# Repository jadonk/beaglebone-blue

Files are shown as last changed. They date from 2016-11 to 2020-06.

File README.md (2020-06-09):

# BeagleBoard.org BeagleBone Blue
_BeagleBone optimized for robotics and machine control_

Home on Github: https://github.com/beagleboard/beaglebone-blue



To optimize BeagleBone for education, BeagleBone Blue was created that integrates many components for robotics and machine control, including connectors for off-the-shelf robotic components. For education, this means you can quickly start talking about topics such as programming and control theory, without needing to spend so much time on electronics. The goal is to still be very hackable for learning electronics as well, including being fully open hardware.

BeagleBone Blue's legacy is primarily from contributions to BeagleBone Black robotics by [UCSD Flow Control and Coordinated Robotics Lab](http://robotics.ucsd.edu/), [Strawson Design](http://www.strawsondesign.com/), [Octavo Systems](http://octavosystems.com), [WowWee](http://www.wowwee.com/mip/), [National Instruments LabVIEW](http://www.ni.com/labview/) and of course the [BeagleBoard.org Foundation](https://beagleboard.org/about).

# Terms
These design materials are *NOT SUPPORTED* and *DO NOT* constitute a reference design. Only “community” support is allowed via resources at [BeagleBoard.org/discuss](https://beagleboard.org/discuss).

THERE IS NO WARRANTY FOR THE DESIGN MATERIALS, TO THE EXTENT PERMITTED BY APPLICABLE LAW. EXCEPT WHEN OTHERWISE STATED IN WRITING THE COPYRIGHT HOLDERS AND/OR OTHER PARTIES PROVIDE THE DESIGN MATERIALS “AS IS” WITHOUT WARRANTY OF ANY KIND, EITHER EXPRESSED OR IMPLIED, INCLUDING, BUT NOT LIMITED TO, THE IMPLIED WARRANTIES OF MERCHANTABILITY AND FITNESS FOR A PARTICULAR PURPOSE. THE ENTIRE RISK AS TO THE QUALITY AND PERFORMANCE OF THE DESIGN MATERIALS IS WITH YOU. SHOULD THE DESIGN MATERIALS PROVE DEFECTIVE, YOU ASSUME THE COST OF ALL NECESSARY SERVICING, REPAIR OR CORRECTION.

In other words, you may use the design materials as you choose and there is no license with regards to usage in the manufacturing process. We mean it, these design materials may be totally unsuitable for any purposes. Don't blame us!

As a general rule, we don't encourage use of this or other off-the-shelf single board computers in commercial products without engaging with a manufacturer to create a supplier agreement and make sure that you can get material as your business demands. Further, we do update the design on occasions where we find it necessary and won't guarantee a supply of older revisions, though we do seek periodic manufacturing of all of our boards for a period of roughly 10 years and will make design changes to replace obsolete parts and that may impact your usage. If you do opt to use it in a product, you take full responsibility for that product.

Do not use the BeagleBoard.org logo or trademarks (such as BeagleBoard and BeagleBone) on your products without a [logo license](https://beagleboard.org/logo) from the BeagleBoard.org Foundation, but feel free to reference BeagleBoard.org.

See the [LICENSE](https://github.com/beagleboard/beaglebone-blue/blob/master/LICENSE) file regarding the copyright of these materials.

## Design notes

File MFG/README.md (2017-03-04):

# PCB fabrication information
* 1.6 mm PCB thickness
* 1 oz copper thickness on outer layers
* 0.5 oz copper on internal layers
* Solder mask as blue
* Silk print as white

# Files
* bb_blue_4layer.cam - EAGLE CAM script
* BeagleBone_Blue.dri - drill log
* BeagleBone_Blue.gpi - outline log
* BeagleBone_Blue.toplayer.ger - top layer copper
* BeagleBone_Blue.internalplane1.ger - inner layer copper
* BeagleBone_Blue.ingernalplane2.ger - inner layer copper
* BeagleBone_Blue.bottomlayer.ger - bottom layer copper
* BeagleBone_Blue.topsilkscreen.ger - top layer silkscren
* BeagleBone_Blue.bottomsilkscreen.ger - bottom layer silkscren
* BeagleBone_Blue.boardoutline.ger - board outline or mill layer
* BeagleBone_Blue.tcream.ger - top layer solder paste
* BeagleBone_Blue.bcream.ger - bottom layer solder paste
* BeagleBone_Blue.topsoldermask.ger - top layer soldermask
* BeagleBone_Blue.bottomsoldermask.ger - bottom layer soldermask
* BeagleBone_Blue.drills.xln - drill file

# Conformal coating application areas

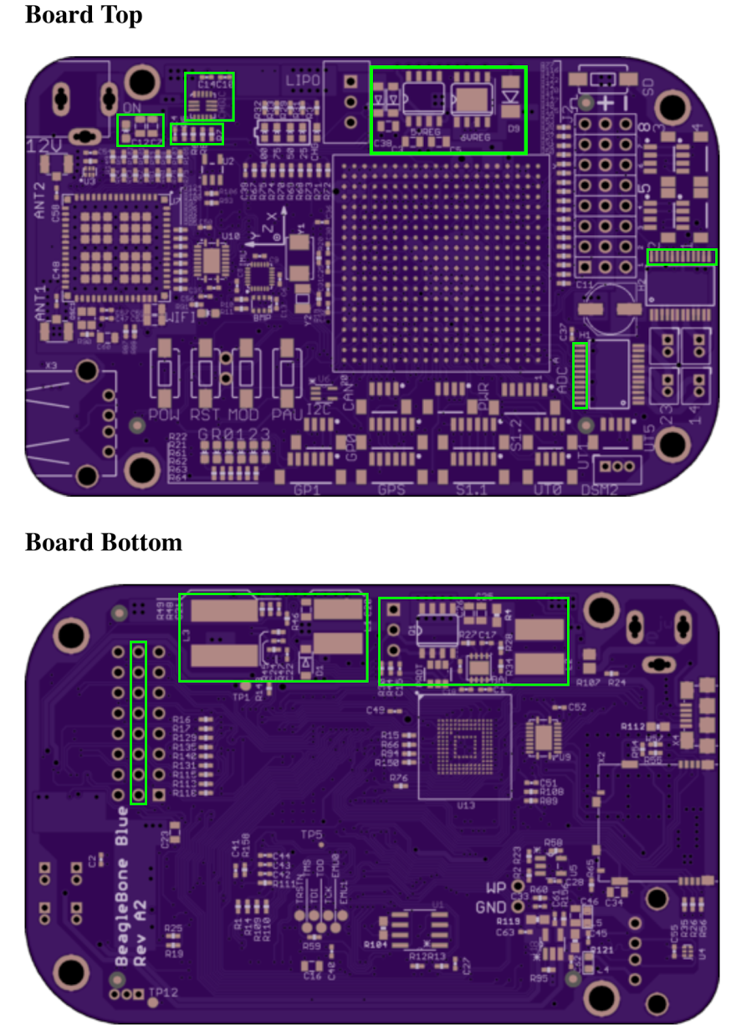
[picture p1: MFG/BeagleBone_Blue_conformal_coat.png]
Image showing conformal coated areas


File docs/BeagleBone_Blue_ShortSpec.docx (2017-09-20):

BeagleBone™ Blue is based on the extremely successful open-source hardware design of BeagleBone™ Black, a high-expansion, maker-focused, community-supported open hardware computer, created by the BeagleBoard.Org Foundation. BeagleBone™ Blue combines the high-performance flexible WiFi/Bluetooth WiLink™ interface of the BeagleBone™ Black Wireless and the robotics capabilities of the Robotics Cape from Strawson Design. BeagleBone™ Blue has onboard 2 cell (2S) LiPo battery management with charger and battery level LEDs, 8 servo motor outputs, 4 DC motor drivers, 4 quadrature encoder inputs, a wide array of GPIO and serial protocol connectors including CAN, a 9 axis IMU and barometer, 4 ADC inputs, a PC USB interface, an USB 2.0 host port, a reset button, a power button, two user configurable buttons and six indicating LEDs. Built on Octavo Systems’ System-In-Package that integrates a high-performance TI ARM processor and 512MB of DDR3, BeagleBone™ Blue boots Linux in around 10 seconds and gets you started developing through your web browser in less than 5 minutes with just a single USB cable.

Specifications:

  a. Processor (Integrated in the OSD3358):
    i. AM335x 1GHz ARM® Cortex-A8
    ii. SGX530 graphics accelerator
    iii. NEON floating-point accelerator
    iv. 2x PRU 32-bit 200MHz microcontrollers
  b. Memory:
    i. 512MB DDR3 800MHZ RAM (Integrated in the OSD3358)
    ii. 4GB 8-bit eMMC on-board flash storage
    iii. SD/MMC Connector for microSD
  c. Software Compatibility
    i. Debian
    ii. Android
    iii. Ubuntu
    iv. Cloud9 IDE on Node.js w/ BoneScript library
  d. Connectivity
    i. High speed USB 2.0 Client port: Access to USB0, Client mode via microUSB
    ii. High speed USB 2.0 Host port: Access to USB1, Type A Socket, 500mA LS/FS/HS
    iii. WiLink 1835 WiFi 802.11 b/g/n 2.4GHz. Supports the following modes
      1. 2x2 MIMO
      2. AP
      3. SmartConfig
      4. STA
      5. Wi-Fi Direct
      6. Mesh over Wi-Fi based on 802.11s
    iv. WiLink 1835 Bluetooth 4.1 with BLE
    v. Serial port:
      1. UART0, UART1, UART5 available via 4 pin JST connectors
      2. UART2 available via 6 pin JST connector (EM-506 GPS style connector)
      3. UART4 RX available via 3 pin DSM2 connector
    vi. I2C1 available via 4 pin JST connector
    vii. SPI1 CS0 (S1.1) and SPI1 CS1 (S1.2) available via 6 pin JST connectors
    viii. CAN available via 4 pin JST connector (includes TCAN1051 CAN transceiver)
    ix. 8 GPIOs (GP0 and GPI1) available via 6 pin JST connectors
    x. ADC inputs 0 to 3 available via 6 pin JST connector
    xi. 3.3VDC and 5VDC power output via 4 pin JST connector
  e. Power management:
    i. TPS65217C PMIC is used along with a separate LDO to provide power to the system (Integrated in the OSD3358)
    ii. 2 cell (2S) LiPo battery charger (powered by 9 – 18VDC DC Jack)
      1. 4 battery level LEDs
      2. 1 charger LED
    iii. 6VDC 4A regulator to drive servo motor outputs
  f. Debug Support: JTAG test points
  g. Power Source
    i. microUSB USB
    ii. 2 cell (2S) LiPo battery connector
    iii. 9 - 18VDC DC Jack
  h. User Input / Output
    i. Power Button
    ii. Reset Button
    iii. Boot Button
    iv. 2 user configurable buttons
    v. 6 user configurable LEDs; Power LED
  i. Motor Control (requires power from either DC Jack or 2S battery):
    i. 4 DC motor drivers
    ii. 4 Quadrature encoder inputs
    iii. 8 Servo motor outputs
  j. Sensors
    i. 9 axis IMU
    ii. Barometer

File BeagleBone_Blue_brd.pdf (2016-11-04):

# BeagleBone Blue

# BeagleBone optimized for educational robotics

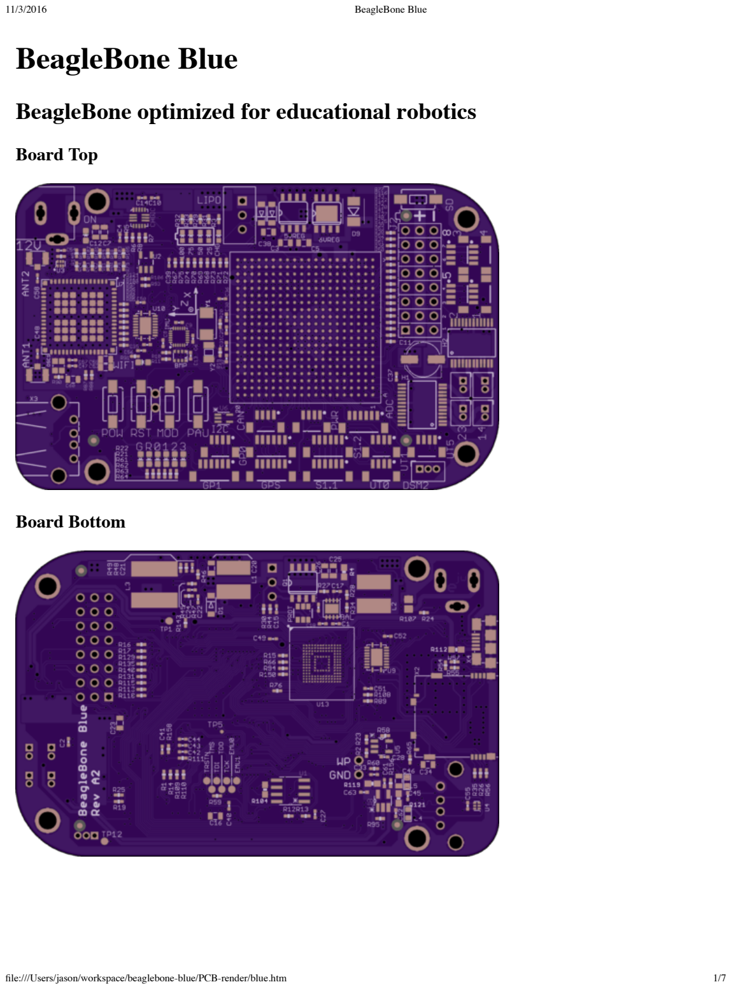
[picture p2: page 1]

11/3/2016 | BeagleBone Blue
file:///Users/jason/workspace/beaglebone-blue/PCB-render/blue.htm | 1/7

# Board Top

# Board Bottom

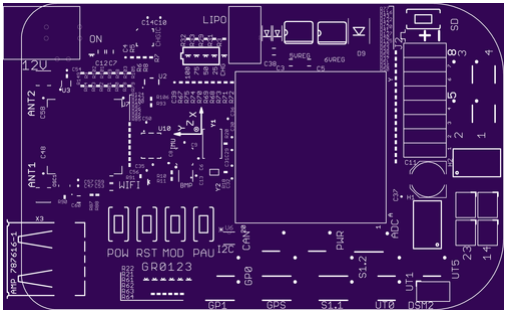
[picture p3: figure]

file:///Users/jason/workspace/beaglebone-blue/PCB-render/blue.htm | 2/7

# Drills

## Rendered from "BeagleBone_Blue.XLN"

# Top Silk Screen

## Rendered from "BeagleBone_Blue.GTO"

file:///Users/jason/workspace/beaglebone-blue/PCB-render/blue.htm | 3/7

# Board Outline

## Rendered from "BeagleBone_Blue.GKO"

file:///Users/jason/workspace/beaglebone-blue/PCB-render/blue.htm | 4/7

# Internal Plane 2

## Rendered from "BeagleBone_Blue.G3L"

# Bottom Silk Screen

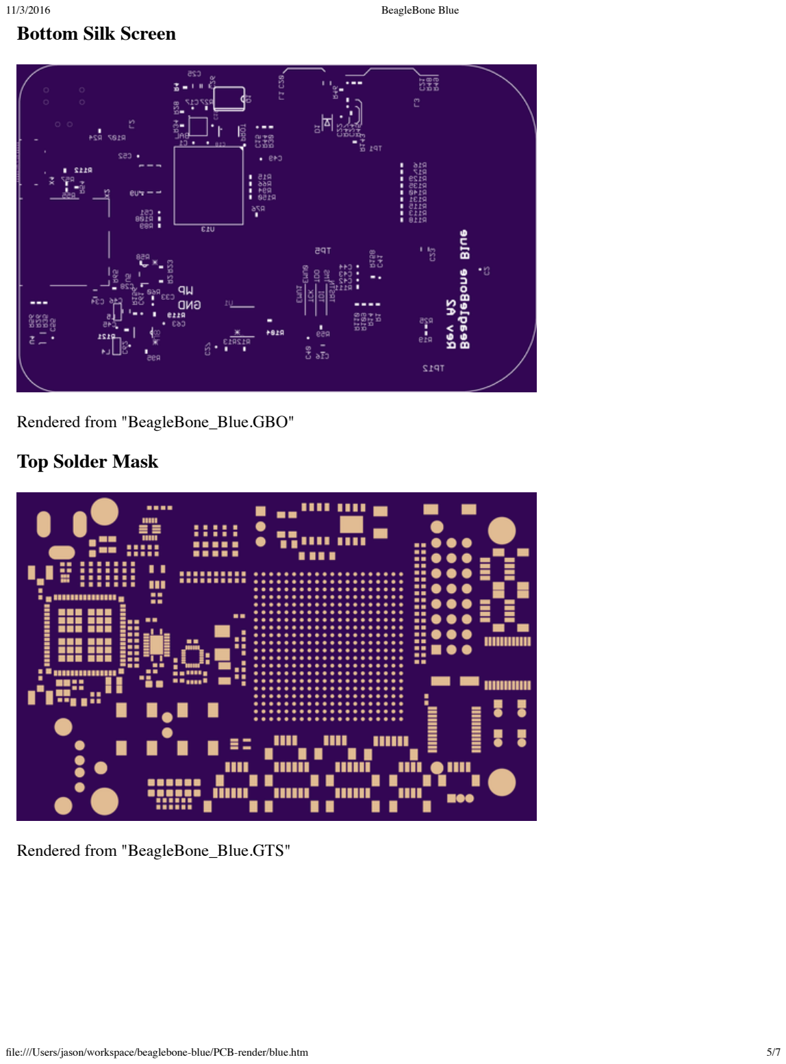
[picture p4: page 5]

file:///Users/jason/workspace/beaglebone-blue/PCB-render/blue.htm | 5/7

## Rendered from "BeagleBone_Blue.GBO"

# Top Solder Mask

## Rendered from "BeagleBone_Blue.GTS"

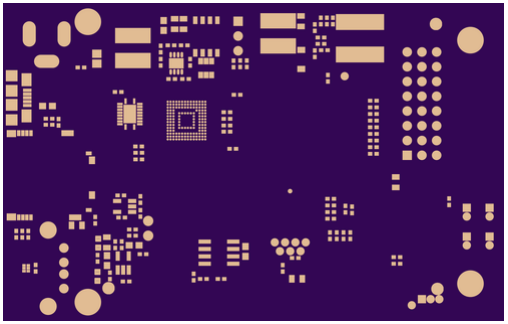
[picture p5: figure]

file:///Users/jason/workspace/beaglebone-blue/PCB-render/blue.htm | 6/7

# Top Layer

## Rendered from "BeagleBone_Blue.GTL"

# Bottom Solder Mask

## Rendered from "BeagleBone_Blue.GBS"

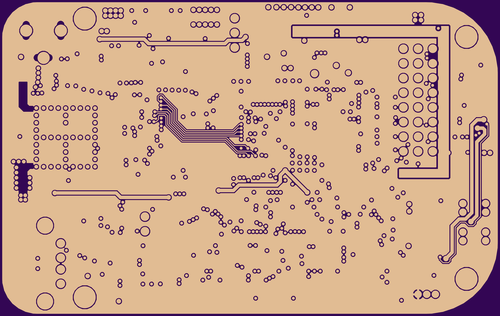
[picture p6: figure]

file:///Users/jason/workspace/beaglebone-blue/PCB-render/blue.htm | 7/7

# Bottom Layer

## Rendered from "BeagleBone_Blue.GBL"

# Internal Plane 1

## Rendered from "BeagleBone_Blue.G2L"

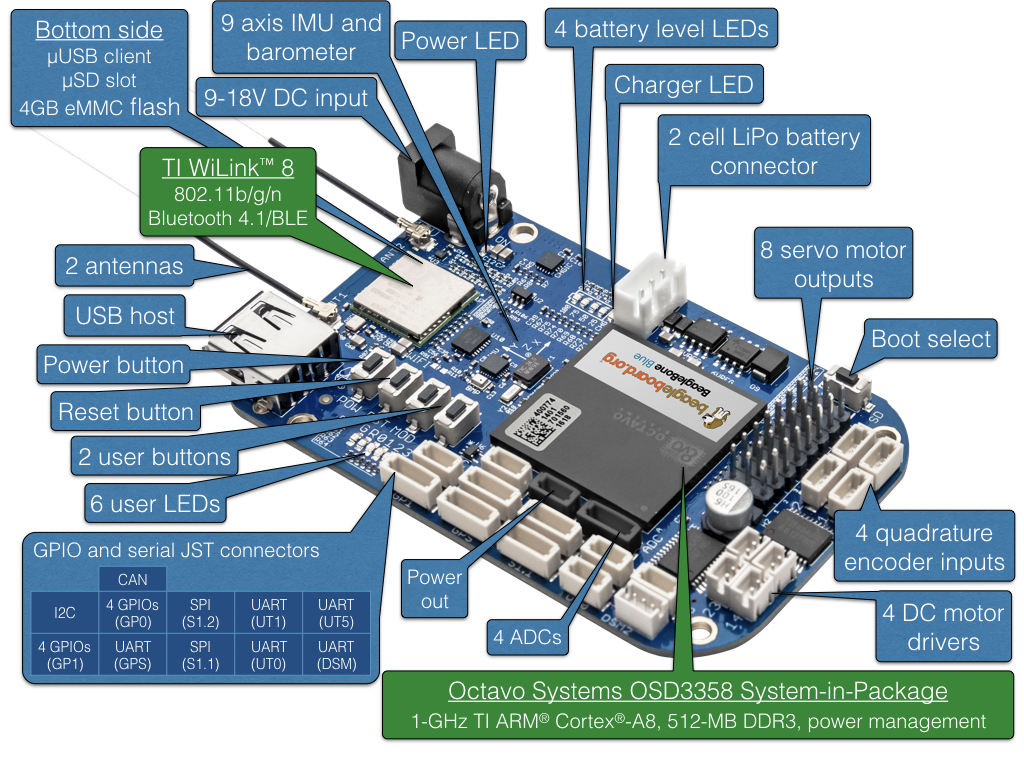
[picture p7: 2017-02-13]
docs/BeagleBone_Blue_balloons.png

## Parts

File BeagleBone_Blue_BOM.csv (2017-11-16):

Qty | Value | Parts | Device | Package | Description | MANUFACTURER AND PART NUMBER | Temperature range / Celsius
5 | BLUE | 0, 1, 2, 3, ON | LED0603 | LED-0603 | LEDs | Lite-On LTST-C191TBKT | -20..80
1 | PJ-102B_POWER_CON | 12V | PJ-102B_POWER_CON | PJ-102B_POWER_CON |  | CUI PJ-102B, MT CONN DC630-20D
1 | AP1509SOIC-8-TIGHT | 5VREG | AP1509SOIC-8-TIGHT | SO08-TIGHT | 150KHz, 2A PWM BUCK DC/DC CONVERTER | Diodes Inc. AP1509-50SG-13 | -20..85
1 | AOZ1284 | 6VREG | AOZ1284 | SO08-EXPOSED |  | Alpha & Omega Semiconductor AOZ1284PI | -40..85
6 | JST_SH_6 | ADC, GP0, GP1, GPS, S1.1, S1.2 | JST_SH_6 | JST_SH_6 |  | JST BM06B-SRSS-TB(LF)(SN), MT CONN WTB10-06-02-2
2 | U.FL-R-SMT-1(10) | ANT1, ANT2 | U.FL-R-SMT-1 | U.FL-R-SMT-1 |  | Hirose U.FL-R-SMT-1(10), MT CONN JTIX-20279
2 | RED | B0, R | LED0603 | LED-0603 | LEDs | Everlight 19-21SURC/S530-A3/TR8, Everlight 19-217/R6C-AL1M2VY/3T
6 | GREEN | B1, B2, B3, CHG, G, WIFI | LED0603 | LED-0603 | LEDs | Everlight 19-21SYGC/S530-E2/TR8, Everlight 19-217/GHC-YR1S2/3T
1 | BQ29209 | BAL | BQ29209 | 8-SON_3X3MM | BQ29209 2-CELL Balance and Overvoltage Protection | Texas Instruments BQ29209DRBR | -40..110
1 | BMP280 | BMP | BMP280 | BMP280 | BOSCH BMP280 Digital Pressure Sensor | Bosch BMP280 | -40..85
32 | 0.1uF | C1, C2, C6, C8, C9, C13, C14, C15, C17, C18, C19, C21, C22, C24, C27, C28, C35, C37, C39, C40, C41, C43, C44, C45, C47, C49, C50, C51, C52, C54, C55, C56 | CAP0402-CAP | 0402-CAP | Capacitor | Samsung CL05A104MP5NNNC, Kemet C0402C104K9PACTU, Murata GRM155R71C104KA88D | -55..85
1 | 100uF 16V | C11 | CPOL-USD | PANASONIC_D | POLARIZED CAPACITOR, American symbol | LELON VES101M1CTR-0605, United Chemi-Con EMVA160ADA101MF55G | -40..85
6 | 10pF | C29, C30, C31, C32, C48, C58 | CAP0402-CAP | 0402-CAP | Capacitor | Yaego CC0402JRNPO9BN100 | -55..125
15 | 10uF | C3, C5, C7, C12, C16, C20, C23, C25, C26, C34, C38, C46, C53, C59, C60 | CAP0805 | 805 | Capacitor | Murata GRM219R61E106KA12D | -55..85
2 | 2.2uF | C33, C36 | CAP0402-CAP | 0402-CAP | Capacitor | TDK C1005X5R0J225K050BC, Murata GRM155R60J225ME15D | -55..85
4 | 1uF | C4, C10, C57, C61 | CAP0402-CAP | 0402-CAP | Capacitor | Samsung CL05A105KO5NNNC, Taiyo Yuden JMK105BJ105KV-F, Murata GRM155R60J105KE19D | -55..85
1 | 1nF | C42 | CAP0402-CAP | 0402-CAP | Capacitor | Murata GRM155R71H102KA01D | -55..85
2 | 0.22uF | C62, C63 | CAP0402-CAP | 0402-CAP | Capacitor | ???
10 | JST_SH_4 | CAN, E1, E2, E3, E4, I2C, PWR, UT0, UT1, UT5 | JST_SH_4 | JST_SH_4_SMD |  | JST BM04B-SRSS-TB(LF)(SN), MT CONN WTB10-04-02-2 | -25..85
1 | MP2615 | CHGIC | MP2615 | MP2615 |  | Monolithic Power Systems MP2615GQ-Z | -40..85
3 |  | D1, D2, D3 | DIODESOD-123 | SOD-123 | Diode | ON Semiconductor MBR230LSFT1G | -55..125
1 |  | D9 | DIODEDO214AA | DO-214AA | Diode | Vishay SSB44-E3/52T | -65..150
1 | JST_ZH_3 | DSM2 | JST_ZH_3 | JST_ZH_3 |  | JST B3B-ZR(LF)(SN), MT CONN WB150SL-03SR03
2 | TB6612FNG | H1, H2 | TB6612FNG | SSOP24 | Toshiba 1A motor driver | Toshiba TB6612FNG(O,C8,EL) | -20..85
1 | MPU-9250 | IMU | MPU-9250 | QFN24G-0.4-3X3MM | 314990005 | Invensense MPU-9250 | -40..105
1 | SERVO_HEADERS_8X | J2 | SERVO_HEADERS_8X | 3X8_0.1_HEADER |  | Preci-Dip 894-80-024-10-001101, Samtec THTSW-108-08-F-T, ??? JTP254-D180-308-001-T | -55..105
2 | 6.8uH | L1, L2 | INDUCTORBOURNS_SRN6045 | SRN6045 | Inductors | Taiyo Yuden NRS6045T6R3MMG | -40..125
1 | 3.6 uH | L3 | INDUCTOR | 8X8MM_INDUCTOR | Inductors | Taiyo Yuden NRS8040T3R6NJGJ | -25..120
2 | 120 | L4, L5 | INDUCTOR/FERRITE-BEAD'0603' | L0603 |  | Laird LI0603G121R-10, Murata BLM18AG121SN1D | -55..125
1 | BATTERY | LIPO | JST_XH_3-PIN | JST_XH_3-PIN |  | MT CONN WB250SV-03SBD03, JST B3B-XH-A(LF)(SN) | -25..85
4 | JST_ZH_2 | M1, M2, M3, M4 | JST_ZH_2 | JST_ZH_2 |  | MT CONN WB150SV-02SBD03, JST B2B-ZR(LF)(SN) | -25..85
5 | SWITCH-MOMENTARY-2SMD-1101NE | MOD, PAU, POW, RST, SD | SWITCH-MOMENTARY-2SMD-1101NE | TACTILE-SWITCH-1101NE | Various NO switches- pushbuttons, reed, etc | C&K Components RS-032G05A3-SM RT | -20..70
1 | NZ2520SB-32.768KHZ-NSA3534C | OSC1 | OSCILLATOR | NZ2520S |  | NDK NZ2520SB-32.768KHZ-NSA3534C, Interquip 1651-L3273-BTKQYA | -40..85
1 | S-8261 | PROT | S-8261 | SOT-236 |  | Seiko S-8261AAJMD-G2JT2G | -40..85
1 | MOSFET-N | Q1 | MOSFET-NCHANNEL | SO08-TIGHT | Common NMOSFET Parts | Vishay Siliconix SI4778DY-T1-GE3 | -55..150
1 | 47k | R45 | RESISTOR0402-RES | 0402-RES | Resistor | Yaego RC0402JR-0747KL | -55..155
2 | 47k 1% | R1, R19 | RESISTOR0402-RES | 0402-RES | Resistor | Yaego RC0402FR-0747KL | -55..155
1 | 120, DNP | R104 | RESISTOR0603 | 0603-RES | Resistor | N/A
1 | .1, 0805 | R107 | R-US_R0805 | R0805 | RESISTOR, American symbol | Yaego RL0805JR-070R1L | -55..125
3 | 0 | R111, R149, R150 | RESISTOR0402-RES | 0402-RES | Resistor | Yaego RC0402JR-070RL | -55..155
1 | 0 | R112 | RESISTOR0603 | 0603-RES | Resistor | Yaego RC0603JR-070RL | -55..155
2 | 0, DNP | R119, R121 | RESISTOR0603 | 0603-RES | Resistor
20 | 33 | R15, R76, R77, R78, R79, R80, R81, R82, R83, R84, R85, R86, R92, R93, R96, R97, R100, R123, R124, R156 | RESISTOR0402-RES | 0402-RES | Resistor | Yaego RC0402JR-0733RL | -55..155
18 | 100k | R16, R17, R47, R87, R88, R113, R115, R116, R118, R120, R122, R125, R127, R129, R131, R135, R140, R143 | RESISTOR0402-RES | 0402-RES | Resistor | Samsung RC1005J104CS, Yaego RC0402JR-07100KL | -55..155
2 | 1M | R18, R20 | RESISTOR0402-RES | 0402-RES | Resistor | Yaego RC0402JR-071ML | -55..155
4 | 1.5K | R2, R23, R58, R106 | RESISTOR0402-RES | 0402-RES | Resistor | Yaego RC0402JR-071K5L | -55..155
8 | 240 | R21, R22, R29, R30, R31, R32, R33, R91 | RESISTOR0402-RES | 0402-RES | Resistor | Yaego RC0603JR-07240RL | -55..155
26 | 10K | R26, R35, R54, R55, R56, R57, R60, R65, R66, R67, R68, R69, R70, R71, R72, R73, R74, R75, R94, R98, R99, R101, R102, R103, R105, R158 | RESISTOR0402-RES | 0402-RES | Resistor | Samsung RC1005J103CS, Yaego RC0402JR-0710KL | -55..155
3 | 150 | R27, R28, R34 | RESISTOR0402-RES | 0402-RES | Resistor | Yaego RC0402JR-07150RL | -55..155
8 | 1k | R3, R44, R46, R61, R62, R63, R64, R90 | RESISTOR0402-RES | 0402-RES | Resistor | Samsung RC1005J102CS, Yaego RC0402JR-071KL | -55..155
1 | 0.1 | R4 | RESISTOR0603 | 0603-RES | Resistor | Samsung RU1608FR100CS, Yaego RL0603FR-070R1L | -55..155
1 | 100k | R47 | RESISTOR0402-RES | 0402-RES | Resistor
1 | 64.9k | R49 | RESISTOR0402-RES | 0402-RES | Resistor | Samsung RC1005F6492CS | -55..155
4 | 10k | R5, R6, R8, R48 | RESISTOR0402-RES | 0402-RES | Resistor
21 | 4.7k | R7, R10, R11, R12, R13, R24, R36, R37, R38, R39, R40, R41, R42, R43, R50, R51, R52, R53, R59, R109, R110 | RESISTOR0402-RES | 0402-RES | Resistor | Samsung RC1005F2610CS, Yaego RC0402JR-074K7L | -55..155
2 | 4.7k 1% | R14, R25 | RESISTOR0402-RES | 0402-RES | Resistor | Samsung RC1005F2610CS, Yaego RC0402FR-074K7L | -55..155
2 | 1K, DNP | R89, R108 | RESISTOR0402-RES | 0402-RES | Resistor | N/A
1 | 10K, DNP | R9 | RESISTOR0402-RES | 0402-RES | Resistor | N/A
1 | OSD3358 | SIP | OSD3358 | OSD3358 | Octavo Systems LLC - OSD3358 Rev A | Octavo Systems OSD3358-512M-BAS | 0..85
1 | TCAN1051HV | U1 | TCAN1051HV | D8 | CAN Transceiver | Texas Instruments TCAN1051HVD | -40..125
1 | EMMC | U13 | EMMC04G-S100-B08U | MICRON_EMMC_153 |  | Micron MTFC4GACAJCN-1M WT, Kingston EMMC04G-S100-B08U | -40..85
1 | SN74LV1T126DBVR | U2 | SN74LV1T126DBVR | SOT23-5 |  | Texas Instruments SN74LV1T126DBVR | -40..125
2 | TPD4S012DRY | U3, U4 | TPD4S012DRYR | SON-6(TI)-DRY |  | Texas Instruments tpd4s012dryr | -40..85
1 | 24LC_32AT-I/OT | U5 | 24LC_32AT-I/OT | SOT95P290X145-5N | IC, I2C Serial EEPROM,SOT-23-5 | Microchip 24LC32AT-I/OT | -40..125
1 | SN74LVC1G07_DCK_5 | U6 | SN74LVC1G07_DCK_5 | DCK5 | Single Buffer/Driver With Open-Drain Output | Texas Instruments SN74LVC1G07DCKR | -40..125
1 | WL1835MODGBMOCR | U7 | WL1835MOD | MOC-100(TI) |  | Texas Instruments WL1835MODGBMOCR | -20..70
1 | TPS2105_DBV_5 | U8 | TPS2105_DBV_5 | DBV5 |  | tps2105_dbv_5 | -40..85
2 | TXS0108ERGYR | U9, U10 | TXS0108ERGYR | R-PVQFN-N20(TI) |  | Texas Instruments TXS0108ERGYR | -40..85
1 | SCHA5B0200 | X2 | SCHA5B0200(ALPS_USD) | SCHA5B0200 |  | Alps SCHA5B0200 | -20..70
1 | USB1 | X3 | USB_HOST_W/CHASSIS_GND | USB_HOST_HORIZONTAL_W/CHASSIS_GND |  | TE Connectivity / AMP 787616-1-P, ??? UBAF-1202 | -55..85
1 | 10118192-0001LF | X4 | 10118192-0001LF | 10118192-0001LF(MICRO-USB-B-AMPHENOL-FCI) | Amphenol FCI Micro USB Type B Complete Surface Mount (SMT) no guide holes | FCI 10118192-0001LF, ??? UBAF-0608 | -30..80
1 | 24 MHz | Y1 | CRYSTAL_5X3.2MM | CRYSTAL_5X3.2MM |  | CTS 445A35A24M00000, TXC 7A-24.000MAAJ-T | -40..85
1 | 32.768kHz | Y2 | CRYSTAL_3.2X1.5 | CRYSTAL_3.2X1.5 |  | Fox Electronics FX135A-327 | -20..70
2 | 2.4GHz antenna |  |  |  |  | Anaren 66089-2406, Gptech GPRC01113-CE0030B5

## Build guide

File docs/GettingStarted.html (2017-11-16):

# Getting Started (Some tips)

## flash firmware

You have probably plugged your board in, and gone to the boards webserver but you want to use something more hands on! 1. Update the firmware to the latest and greatest instructions here (http://192.168.1.7/bone101/Support/BoneScript/updates/) One thing the instructions don't mention is that you need to edit a file in the boot directory in order for the sdcard to be flashed onto the firmware.

1. edit /boot/uEnv on the sdcard.
2. Change ##enable Generic eMMC Flasher: ##make sure, these tools are installed: dosfstools rsync #cmdline=init=/opt/scripts/tools/eMMC/init-eMMC-flasher-v3.sh to ##enable Generic eMMC Flasher: ##make sure, these tools are installed: dosfstools rsync cmdline=init=/opt/scripts/tools/eMMC/init-eMMC-flasher-v3.sh
3. Eject the sdcard from you computer and put it in your Beagle Blue Bone
4. Hold the update button (the one by itself) along with the reset, then let go of the reset, and then the upgrade. This tells the board to boot off the sdcard, with your instruction to flash the sdcard onto the boards firmware.

The flashing only takes a couple of minutes.

## terminal on the board

If you don't have ssh installed, install it. (google is your friend) Then ssh debian@192.168.7.2 The board will tell you what the password is, on my it was temppwd To change your password use the command passwd it will ask you what your current password is, and then ask for the replacement. Then it will say it was too simple and you have to do it again. Normal stuff. If you want to use your simple password, try this.

1. sudo -s

(become superuser/root)

2. enter your password
3. passwd debian
4. exit

(exit from superuser/root)

When you are running as root, passwd is more compliant and will accept simple passwords.

## Want wifi?

On my network, I'm set up as ip 192.168.1.*. To turn your wifi on, do the following.

1. sudo -s

(become superuser/root)

2. cd /etc/network/
3. ifconfig

(Note the wifi inet address, if it is already set, you are done!)

4. connmanctl tether wifi off enable wifi scan wifi services (at this point you should see your network appear along with other stuff, in my case it was "AR Crystal wifi_f45eab2f1ee1_6372797774616c_managed_psk")
5. nano interfaces

(or whatever editor you like)

6. remove the comment # from the wifi lines so it now appears like ##connman: WiFi # connmanctl connmanctl> tether wifi off connmanctl> enable wifi connmanctl> scan wifi connmanctl> services connmanctl> agent on connmanctl> connect wifi_f45eab2f1ee1_6372797774616c_managed_psk connmanctl> quit
7. exit
8. note that you will need to fill in your own network data

## static ip address

You will usually want to have a fixed ip if you are doing robotics, so you have a standard ip to connect to. In my case I wanted 192.168.1.7 to do this,

1. sudo -s
2. connmanctl config wifi_f45eab2f1ee1_6372797774616c_managed_psk --ipv4 manual 192.168.1.7 255.255.255.0 192.168.1.1
3. exit

substitute your own wifi connection of course, and use your own ip as desired.

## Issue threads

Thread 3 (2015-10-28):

Add I/O protection

jadonk, 2015-10-28:
* Add series resistor to I/Os
* Add (DNP) zener diods to I/Os

erikwelsh, 2016-09-27:
Not scheduled to be fixed in any revision.

Closed 2016-10-10.

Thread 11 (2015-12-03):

Add header for UART0

jadonk, 2015-12-03:
* Use a 4-pin JST like the other UART ports.
* No hardware handshaking.

erikwelsh, 2016-09-27:
Rev A1 has a 4-pin JST connector for UART0.

Closed 2016-10-10.

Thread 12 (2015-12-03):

Add series resistors for I/O ports

jadonk, 2015-12-03:

erikwelsh, 2016-09-27:
Same a Issue #3 .  Not scheduled to be fixed in any revision.

Closed 2016-10-10.

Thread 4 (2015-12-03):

Swap UART5_RX and MDIR_2B

jadonk, 2015-12-03:
This is to try to match the UART5 mux. The TI Pin Mux Utility reports an error without this change.

Was the existing wiring verified?

jadonk, 2016-09-20:
Still broken in rev A1.

Closed 2016-11-02.

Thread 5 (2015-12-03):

Adjust SPI1 pins

jadonk, 2015-12-03:
- Use UART0_RTSN (E17) for SPI1_CS0, moving from pin C12.
- Use pin A15 for SPI1_CS1, moving from pin C18.

jadonk, 2016-09-20:
What wasn't noted that I/O set had to have been followed. This will be deferred to Rev B.

erikwelsh, 2016-10-13:
To fix the SPI chip select IO set issue, we will change the location of SPI1 CS0 and CS1.  The final pin mapping will be:

spi1_sclk		A13 (mcasp0_aclkx – current pin)
spi1_d0		B13 (mcasp0_fsx – current pin)
spi1_d1		D12 (mcasp0_axr0 – current pin)
spi1_cs0		H18 (rmii1_refclk – currently unused on BB Blue)
spi1_cs1		C18 (eCAP0_in_PWM0_out – currently GPIO_0_3 on BB Blue)
GPIO_0_3		C12 (currently spi1_cs0)
WIFI_LED		A15 (currently spi1_cs1 - See Issue #29 )

jadonk, 2016-10-13:
There must be an error. How do you have 2 pins be GPIO0_3?

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

erikwelsh, 2016-10-13:
Sorry if I was not clear.  The items in quotes was what the function was on Rev A1a.  Basically, we are taking four pads:  H18, C18, C12 and A15 and swapping around the functionality.  The Rev A2 mapping is outside the quotes.  For example, on Rev A1a GPIO_0_3 (ie GPIO connector 0 pin 3, not AM335 GPIO0_3) was C18.  For Rev A2 it will be C12.

jadonk, 2016-10-16:
@erikwelsh @StrawsonDesign Objections to me changing the net names to reflect the processor GPIO number? I like to avoid people needing to refer to additional documentation in order to program the hardware.

Closed 2016-11-02.

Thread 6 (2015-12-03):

Grab McASP0 for Bluetooth A2DP I2S interface

jadonk, 2015-12-03:
* Move MDIR_1A from U18 to P9_12 (C12) to get MCASP0_ACLKR
* Move LED_2 from V12 to P8_32 (T5) to get MCASP0_FSR
* Move USB1_OCn from T16 to GPIO2_21 (M16) to get MCASP0_AXR0
* Remove HDMICLK_DISn from V17 to get MCASP0_AXR1
* Remove HDMI_INT from U16, just in case I need to get MCASP0_FSX

jadonk, 2016-06-07:
I've confirmed that the McASP connection is not required for connecting to Bluetooth speakers.

erikwelsh, 2016-09-27:
In Rev A1, BT audio signals are hooked up to McASP0 with the following pins:
- MCASP0_ACLKR - pin U18
- MCASP0_FSR - pin V12
- MCASP0_AXR0 - pin T16
- MCASP0_AXR1 - pin V17

The WL183x did not need MCASP0_FSX.  Therefore, it was not connected.

jadonk, 2016-10-10:
BeagleBone Green Wireless .dts file has some info on getting this configured. I'm not sure how to get the device in the right mode to verify this functionality.

Closed 2016-10-10.

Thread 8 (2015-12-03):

Address concerns about connector choice

jadonk, 2015-12-03:
* Could we bundle pig-tails?
  * estimate about $0.10 cost each and likely to bundle about 6 of them
  * 6-wire: https://www.sparkfun.com/products/10361
  * 4-wire: https://www.sparkfun.com/products/9916
  * 2-wire: https://www.sparkfun.com/products/9914
* Where is the documentation for where to buy them?

Why we like them:
* small
* easy to plug and remove
* stay connected well
* readily available

jadonk, 2016-10-12:
We'll have a solution for pigtails and are happy with these connectors.

jiffyjeff, 2022-02-17:
> We'll have a solution for pigtails and are happy with these connectors.

With all due respect, I'd appreciate some assistance locating a bundle of these connectors.

Closed 2016-10-12.

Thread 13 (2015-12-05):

Add CAN PHY and connectors

jadonk, 2015-12-05:

erikwelsh, 2016-09-27:
Rev A1 has CAN PHY (TCAN1051HV) and a JST connector for DCAN1.

jadonk, 2016-10-10:
May need to revisit pin connections. Does that need discussion here before closing this item?

StrawsonDesign, 2016-10-11:
I like the JST connector, think this can be closed.

Dept. Mechanical & Aerospace Engineering
University of California, San Diego

On Mon, Oct 10, 2016 at 11:04 AM, Jason Kridner <notifications@github.com>
wrote:

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

Closed 2016-10-12.

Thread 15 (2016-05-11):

Add connector for additional GPIOs

jadonk, 2016-05-11:

erikwelsh, 2016-09-27:
Rev A1 has two GPIO connectors:
- GPIO0:  4 GPIO pins (JST connector)
- GPIO1: 2 GPIO pins (Grove connector)

GPIO0 uses the following pins (may change in Rev A2):
- Bit 0:  Pin U16 - GPIO1_25
- Bit 1:  Pin V14 - GPIO1_17
- Bit 2:  Pin D13 - GPIO3_20
- Bit 3:  Pin C18 - GPIO0_7

GPIO1 uses the following pins (may change in Rev A2):
- Bit 0:  Pin J15 - GPIO3_2
- Bit 1:  Pin H17 - GPIO3_1

Closed 2016-10-10.

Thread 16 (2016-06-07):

Make new connectors as JST instead of Grove

jadonk, 2016-06-07:

jadonk, 2016-07-19:
Done as part of 57fd393b58db450caf035d6a3a34a7a32e0dd2d6

erikwelsh, 2016-09-27:
Rev A1 has Grove connectors for:
- UART5 (broken due to IOSet issue)
- I2C1
- GPIO (2 pins)

jadonk, 2016-10-12:
Move to JST connectors to save board space and collapse component list.

erikwelsh, 2016-11-01:
Changed UART5 and I2C1 to 4 pin JST connectors.
Changed GPIO1 to a 6 pin JST connector (includes 2 GPIO pins as well as the Red and Green LED signals)

Scalpel78, 2017-03-17:
What is the type of JST connector used called?

StrawsonDesign, 2017-03-17:
All the little I2C, UART, GPIO, SPI, Encoder, and CAN connectors are JST SH, 4 or 6 pin.

Closed 2016-11-02.

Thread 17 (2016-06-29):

Convert client port to OTG

jadonk, 2016-06-29:

jadonk, 2016-06-29:
Use 100mA FET based on ID signal to provide power.

erikwelsh, 2016-09-27:
Not done in Rev A1.

jadonk, 2020-06-09:
Issue migrated to beagleboard/beaglebone-blue#47

Closed 2020-06-09.

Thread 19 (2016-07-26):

Place XYZ silkscreen

jadonk, 2016-07-26:

erikwelsh, 2016-09-27:
Currently, on Rev A1.  Can be closed.

jadonk, 2016-10-10:
It is still a bit small, but it is probably the best we can do.

Closed 2016-10-10.

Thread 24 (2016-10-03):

Change barrel jack from 2.5x5.5mm to 2.1x5.5mm

StrawsonDesign, 2016-10-03:
2.5x5.5mm barrel jacks are far less common than the 2.1x5.5mm standard and are incompatible with the DC adapters found on Sparkfun.com, ebay, and amazon.

jadonk, 2016-10-12:
Error was only on the hand-made prototype. E14 prototypes have the right connector.

Closed 2016-10-12.

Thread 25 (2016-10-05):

Change connection and color of WiFi EN LED

jadonk, 2016-10-05:
It would be easier to identify the WiFi EN and BT EN LEDs if the BT LED was blue and the WiFi LED was green/yellow or some other color. Since we already have green LEDs on the board, perhaps that would be best.

Are these LEDs really all that useful if they are always on? They were helpful for initial debug, but it seems adding additional GPIO LEDs that could be bound to actual network state/activity would be more useful if other GPIOs can be found.

jadonk, 2016-10-12:
Duplicate with #29

Closed 2016-10-12.

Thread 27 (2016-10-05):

Grove connector is wrong part number

jadonk, 2016-10-05:
The JST connectors are not compatible with the Grove cables. Seeed Studio has quoted some SMD versions of their connector.

jadonk, 2016-10-12:
We'll move to smaller JST connectors and use an adapter wire harness.

Closed 2016-10-12.

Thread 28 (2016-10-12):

Are alternate colors available for the JST connectors?

jadonk, 2016-10-12:
This would be to assist in new users locating specific connectors.

erikwelsh, 2016-11-01:
Here is the color scheme for the connectors:

2 pin
M1-4: (4x) white

3 pin
DSM2: (1x) white

4 pin
E1-4, I2C: (5x) white
UT0, UT1, UT5: (3x) black
PWR: (1x) new color #1 (red preferred)
CAN: (1x) new color #2 (green preferred)

6 pin
S1.1, S1.2: (2x) white
GP0-1: (2x) black
ADC: (1x) new color #1 (red preferred)
GPS: (1x) new color #2 (green preferred)

Unfortunately, the colored connectors are a 50% premium over the other connectors so one goal of the above scheme was to minimize the number of colored connectors.

jadonk, 2016-11-15:
If the only secondary color we have is black, let's use white on everything except using black on PWR and ADC. Those are the ones most likely to damage something if connected mistakenly.

cstiegman, 2016-11-15:
Got it - thanks!

Regards,
Craig Stiegman
element14
(773) 90<tel:(773)%20907-5941>7-5941<tel:(773)%20907-5941>

On Nov 15, 2016, at 11:35 AM, Jason Kridner <notifications@github.com<mailto:notifications@github.com>> wrote:

If the only secondary color we have is black, let's use white on everything except using black on PWR and ADC. Those are the ones most likely to damage something if connected mistakenly.

—
You are receiving this because you are subscribed to this thread.
Reply to this email directly, view it on GitHub<https://github.com/jadonk/beaglebone-blue/issues/28#issuecomment-260709970>, or mute the thread<https://github.com/notifications/unsubscribe-auth/AHehhCeqBfeAYJ8UB_gX4odB07LfG4oXks5q-e0EgaJpZM4KVMYC>.
********************************Disclaimer***********************************
The preceding e-mail message (including any attachments) contains information
that may be confidential, be protected by the attorney-client
or other applicable privileges, or constitute non-public information. It
is intended to be conveyed only to the designated recipient(s). If you are
not an intended recipient of this message, please notify the sender by
replying to this message and then delete it from your system. Use,
dissemination, distribution, or reproduction of this message by unintended
recipients is not authorized and may be unlawful.
*****************************************************************************

winsurfwon, 2018-03-16:
Is there a list of all male connectors for all the BB Blue, and is there any MFG that actually sell a set of them minus the power connectors and USB.  It is well specified in the glossy print, but not the actual male mfg connector lead part numbers if one exists.  I called a few but they were not ready for it. So good so far.

jadonk, 2020-06-09:
Issue migrated to beagleboard/beaglebone-blue#52

Closed 2020-06-09.

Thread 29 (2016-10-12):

Change WL_EN LED color to green

jadonk, 2016-10-12:

jadonk, 2016-10-12:
Also, move this LED to the last GPIO rather than WL_EN and make it a general "network connection status" LED.

erikwelsh, 2016-11-01:
Moved WIFI LED to pin A15 (GPIO0_19).  Changed color to Green.

Closed 2016-11-02.

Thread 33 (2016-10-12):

Adjust to fit in Altoid's tin

jadonk, 2016-10-12:

erikwelsh, 2016-11-01:
Moved power connector in as much as possible.  I think it should fit but will not know until we get the A2 boards back.

jadonk, 2016-11-02:
Still would like to find a shorter power connector.

jadonk, 2016-11-07:
I've ordered some PCBs from OSH Park to do a mechanical mock-up to verify the fix. I've not identified a source of a shorter power connector.

jonnycowboy, 2016-11-16:
Would implementing issue 39 (new BMS) allow us to use a different power connector? Is the barrel jack currently used to charge the battery or is it used for directly powering the processor?
https://github.com/jadonk/beaglebone-blue/issues/39

StrawsonDesign, 2016-11-17:
The barrel jack is primarily for charging the battery but can provide power to the 5V regulator when no battery is connected. We picked this connector because of how ubiquitous 12v wallwarts are with this 5.5mm barrel jack. I just wish there were half-length jacks available.

jadonk, 2016-12-08:
I've not been able to find a shorter jack, which is very surprising to me.

A2 still does NOT fit in an Altoids tin. :-(

jadonk, 2017-02-09:
@StrawsonDesign For rev B, can we switch the power input to a JST connector?

https://www.sparkfun.com/products/8734

I wonder how much it would cost to include that in the kit. :-/

StrawsonDesign, 2017-02-10:
Hmmmm, sorry but I really really like the universal barrel jack. We would
get so much pushback from people complaining about needing dedicated
adapters just to charge the thing just like Apple gets with their headphone
jack adapters. I do adore the Altoids tin concept, don't get me wrong! But
in practice I don't think anyone is running their board in a conductive
tin, whereas everyone will need to charge it and everyone with a wifi
router has one of these 12v dc wallwarts in their home already.

Charging via a 9v or 12v capable USB-C connector may get initial pushback
too but at least that's looking a bit more towards a future universal
standard.

Respectfully,
James

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

jadonk, 2020-06-09:
Issue migrated to beagleboard/beaglebone-blue#50

Closed 2020-06-09.

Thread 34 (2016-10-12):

USB host won't work when powered over USB client

jadonk, 2016-10-12:

Closed 2016-10-12.

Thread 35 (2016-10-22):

Change 6V_REG soft-start cap to 0.1uf

StrawsonDesign, 2016-10-22:
6V_REG works on cape but only starts when no load is present on Blue. Cause is likely the 1nF capacitor C21 on Blue. Should change to 0.1uF to match cape.

erikwelsh, 2016-11-01:
Updated schematics and BOM to change the value of C21.

jadonk, 2016-11-02:
Can we modify a board to confirm?

StrawsonDesign, 2016-11-02:
I'll have a go tomorrow.

On Tue, Nov 1, 2016 at 7:38 PM, Jason Kridner <notifications@github.com>
wrote:

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

StrawsonDesign, 2016-11-04:
confirmed, the capacitor change fixes soft-start

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

jadonk, 2016-11-04:
@StrawsonDesign Thanks!!

Closed 2016-11-04.

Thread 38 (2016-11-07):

Need spec on conformal coating

jadonk, 2016-11-07:

StrawsonDesign, 2016-11-08:
MG chemicals 419D Acrylic Conformal Coating was my original suggestion to Embest. However they used Humiseal 1B73 which is an almost identical product and seems to have worked well on our prototypes.

jadonk, 2016-11-15:
@StrawsonDesign What areas on the A2 layout? Can you mark-up the board PDF?

jadonk, 2016-11-22:
Graphic added... https://github.com/jadonk/beaglebone-blue/commit/432ebf36c79731519eb745985146eb871d6f98e4

Now we just need to add related information to the README.md in the MFG directory and we can close this issue.

jadonk, 2020-06-09:
Issue migrated to beagleboard/beaglebone-blue#49

Closed 2020-06-09.

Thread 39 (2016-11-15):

Update to use lower-cost battery management

jadonk, 2016-11-15:
http://www.ti.com/tool/TIDA-00982#Technical Documents

jadonk, 2020-06-09:
Issue migrated to beagleboard/beaglebone-blue#48

Closed 2020-06-09.

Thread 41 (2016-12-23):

MPU 9250 via SPI

mirkix, 2016-12-23:
Hi, is it an option to connect the MPU 9250 via SPI and not via I2C? With Ardupilot we can sample at 4 kHz / 8 kHz (acc gyro) in this case I2C is not fast enough for the data transfer. It is possible to sample slower too, than the transfer speed via I2C should be okay.

StrawsonDesign, 2016-12-28:
Hi Mirko,

Sadly the 9250 is on the I2C bus on both Blue and Cape. In my flight code I
use the 9250's DMP for quaternion orientation estimation and also use the
DMP's fixed-rate interrupt function (up to 200hz only) to generate the
timing for the discrete feedback loop. Pulling accel, gyro, mag, and
quaternion data at 200hz puts the i2c bus at about %15 use when taking
advantage of the 9250's FIFO buffer to do one big read at a time.

I have no doubt sampling just the accel, and gyro 1khz would be possible
over I2C with intermittent reads to the magnetometer. However, even on a
small quadcopter the crossover frequency for the roll/pitch feedback
controllers is only around 10-20hz so I've found 200hz sample rate to be
more than sufficient for smooth feedback control. Anything faster is
difficult to achieve in userspace linux without multiple cores anyway.

Best,
James

Dept. Mechanical & Aerospace Engineering
University of California, San Diego

On Fri, Dec 23, 2016 at 10:10 PM, Mirko Denecke <notifications@github.com>
wrote:

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

mirkix, 2016-12-28:
@StrawsonDesign Hi James, is there any documentation free available about the DMP? I think ArduPilot try to sample as fast as possible to avoid problems caused by vibrations (aliasing).
I am working on ArduPilot support for the Blue and made good progress so far.

Regards
Mirko

jadonk, 2017-01-13:
@mirkix @StrawsonDesign shall I try to ping Invensense on the DMP documentation issue?

StrawsonDesign, 2017-01-13:
Hi Mirko, Jason,

Free documentation on the DMP is limited to their example code and a
pamphlet with a brief overview of functionality. I've played with the DMP a
lot over the past few years and I think I've gotten as much performance out
of it as I can having written my implementation %75 from scratch. I even
managed to get it to package the magnetometer data into the same FIFO
packet as the DMP, accel, and gyro data which a comment in Pansenti's
mpu9250 driver said was "impossible". The sparkfun library is horrifically
slow and does a lot of unnecessary register modifications every time it
swaps between reading mag and dmp.

The DMP is internally limited to 200hz, presumably because it has to do a
LOT of floating point arithmetic for it's quaternion estimate. It always
samples and runs its filter at 200hz, even if you set up the interrupt
signal to run as a divisor of that. Sadly, that also means that the accel
and gyros have to be set to sample at 200hz too, so pinging them between
DMP reads is useless.

I understand your worry about aliasing, but 200hz is still 20x faster than
the crossover frequency of even my fastest feedback controller. A properly
designed compensator (eg not PID!) will have gain roll-off well before
200hz.

Best,
James

On Fri, Jan 13, 2017 at 8:11 PM, Jason Kridner <notifications@github.com>
wrote:

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

jadonk, 2017-01-24:
@mirkix Can you confirm you are comfortable with @StrawsonDesign's answer?

mirkix, 2017-01-25:
@jadonk :+1:

jadonk, 2020-06-09:
Issue migrated to beagleboard/beaglebone-blue#43

Closed 2020-06-09.

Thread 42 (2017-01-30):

Pin table needs to be updated

jadonk, 2017-01-30:
Commits 4e067f5e1d7aef13628bb9526eb36e3b84eef1b9 and f9327dfb45372d406d32ded716de87cc40be3364 corrupted the XML file. I plan to convert the XML file to CSV and request that @StrawsonDesign re-applies the changes and have @erikwelsh assist in confirming the document against the design.

jadonk, 2020-06-09:
Issue migrated to beagleboard/beaglebone-blue#36

Closed 2020-06-09.

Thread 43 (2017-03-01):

BT_EN is not an LED

dlech, 2017-03-01:
I was checking out the LEDs and noticed that there is an LED named `wl18xx_bt_en` that is not actually an LED. It is defined in [am335x-boneblue-wl1835.dtsi](https://github.com/beagleboard/linux/blob/4.4/arch/arm/boot/dts/am335x-boneblue-wl1835.dtsi#L17). Was this an LED in previous revisions of the board? I have rev A2.

dlech, 2017-03-01:
Also reported this at https://github.com/beagleboard/linux/issues/118

jadonk, 2017-03-02:
It was an LED in previous revisions. It is still configured as an LED to provide simple controls.

Closed 2017-03-02.

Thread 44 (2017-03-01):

Schematic text is not searchable

dlech, 2017-03-01:
It would be helpful to be able to search for text in the pdf version of the schematic. You can fix this by going to *Options > User Interface...* in Eagle and unchecking *Always vector font* and *Persistent in this drawing*, then print to PDF.

jadonk, 2017-03-04:
Fixed. Thanks for the help on how to do this.

Closed 2017-03-04.

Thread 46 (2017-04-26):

Getting Started

adanmaa, 2017-04-26:
Had this board for a day.  Powered it on and opened the getting started page.  RNDIS tethering doesn't work on OS X Yosemite.  Serial connection doesn't work unless you download full drivers from FTDI.  I tried accessing beagle bone access point but don't know the password.  Was able to login through the terminal with default password, but don't know how to update software without network connection.  Now beagle bone doesn't seem to be working -  not able to browse device files in Finder window; won't connect serially; can't see access point; and RNDIS won't work.  Any other way to access beagle bone?

jadonk, 2017-04-27:
Password is "BeagleBone". Update software using http://bbb.io/latest.

3space, 2017-04-27:
How do I boot old image from flash again?

jadonk, 2017-04-27:
Remove the SD card and you'll boot from the on-board flash again.

jadonk, 2017-04-27:
For USB interface via Yosemite, have you tried 192.168.6.2?

3space, 2017-04-27:
192.168.6.2 works. What is the password to ssh into root account?

jadonk, 2017-05-16:
ssh to root is disabled. ssh as debian and then do 'sudo -s'.

OscarJGV26, 2017-09-01:
I have problems to apt-get update and git clone anything... It says connection refused on port 443.

I am already able to ping 8.8.8.8 and www.google.com.

I am sharing the internet through my computer with /sbin/route add default gw 192.168.7.1 (see derek maloy usb network). I do it like this and not through wifi because I can't get wifi to work on thee university network (eduroam) and I have since there is a problem with this type of networks (IEEE8021x).

Could I get some help with this please? It's driving me nuts that I can't git clone anything.

jadonk, 2020-06-09:
Issue migrated to beagleboard/beaglebone-blue#44

Closed 2020-06-09.

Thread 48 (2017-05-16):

Battery drains when power is disabled

jadonk, 2017-05-16:
Battery should not drain when device is powered down.

jadonk, 2020-06-09:
Issue migrated to beagleboard/beaglebone-blue#42

Closed 2020-06-09.

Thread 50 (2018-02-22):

OSD3358 so week?

h2mille, 2018-02-22:
Hi,
This is my second broken BBBlue, breaking "the same way" I do have 5V line working, but not 3.3V anymore. I just understood the regulator is inside OSD3358 SIP A, and so part of the main chip, that I'm really unable to replace.
For once, I saw my BBB breaking (last time, it didn't boot after no use for a while): a bit intensive usage of two motors (on H1). ANyway, now, the ib led blink  once a  quater second, and disapear. I disconnected the 3.3V pin on h1, still not working. So now... Why the 3.3 power is going through the main processor, instead of going through a succincte regulator?( for the driver, and for output lines too.

At last, is it possible to get a new board Asap? my supplyer will think I'm just bad, and might be lazy to change my boards, as: I broke (but repaired) the usb connector, got this 3.3V problem twice, got the flash  chip burnt one day after getting it (really heating a lot, still can boot a bit on SD), and at last got Q1 burnt (no reason, I changed it this morning)

jadonk, 2018-03-02:
Q1 will fry if you connect the LiPo battery backwards. Contact me via e-mail, calendar appointment if needed. https://beagleboard.org/about.

Closed 2018-03-02.

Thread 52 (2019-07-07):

Wrong voltage on JST connectors ?

GDV0, 2019-07-07:
Hello,

Working with a Beaglebone Blue rev A2, I have measured 5V on UART  and  EQEP encoder connectors, which is not consistent with the 3V3 defined in the schematic.

jadonk, 2020-06-09:
Issue migrated to beagleboard/beaglebone-blue#35

Closed 2020-06-09.

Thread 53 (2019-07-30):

Beaglebone Blue: Pull PWM Pins Low on Boot

ansarid, 2019-07-30:
Currently we have a large robot that is using the GPS UART-RX and UART-TX as PWM outputs for an H-Bridge that only allows a PWM logic level of 5.5v max (this is why we are not using the on board motor outputs). During boot our PWM pins get pulled high which is an issue because it causes the robot to start moving.

Is there a way to configure pins to stay low on boot to avoid this issue?

jadonk, 2020-06-09:
Issue migrated to beagleboard/beaglebone-blue#46

Closed 2020-06-09.

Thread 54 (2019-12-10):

Drivers of the motors are insufficiently protected for over-current

dorovl, 2019-12-10:
According to the datasheet of the TB6612FNG circuit have an output current: IOUT = 1.2 A(ave)/3.2 A (peak) but also a built-in thermal shutdown circuit. I first measured the running (0.2 A) and starting current (1.2 A) of my motors and then connected them to the board.

I tested the motors with "rc_test_motors" program from Robot Control Library and this worked fine. Meanwhile, I also added the "-s {duty}" argument which sweeps motors back and forward at duty cycle. I applied for test a very short duty cycle of level 1, which induced a very high current and the burned-out the driver IC.

In a pernicious way, after the incident, the drivers IC are sinking a very high current (dissipating a lot of heat) which caused a malfunction of the eMMC (read only file system). To continue to operate my BeagleBone, it was necessary to undersold the driver ICs with hot air. However, the conformal coating material was infiltrated between the circuit and the PCB making undersoldering impossible without raising the air hot temperature over 400 °C. This damaged the plastic connectors nearby, but my BeagleBone is still working.

- **We recommend to use a fast current limiter because it seems that the built-in thermal shutdown circuit has in not fast enough for transient effects over-current protection.**

jadonk, 2020-06-09:
Issue migrated to beagleboard/beaglebone-blue#38

Closed 2020-06-09.

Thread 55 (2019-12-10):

The two black JST-SH connectors don't have a retention bed, unlike the white JST-SH connectors

dorovl, 2019-12-10:
The connector that plugs inside is not retained. By vibrations, this connector comes out and this is particularly dangerous in the context of a flight controller (our project).

Please note I'm referring to the "Power out" and "4 ADC" connectors (see red arrow):

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

- **We recommend to put also a white JST-SH connectors on the next version.**

jadonk, 2020-06-09:
Issue migrated to beagleboard/beaglebone-blue#45

Closed 2020-06-09.

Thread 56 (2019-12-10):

WiFi antenna attachment

dorovl, 2019-12-10:
We had a bad signal intensity (as we where quite far from the router). Therefore, we tried to take out the WiFi antenna to obtain a better a signal intensity. Lot of pictures like https://github.com/beagleboard/beaglebone-blue/blob/master/docs/BeagleBone_Blue_balloons.png illustrate BBBL with the antenna out. Therefore, we don't saw any constraints to rotate the antenna.

To rotate the antenna there are two options:

1. Rotate the antenna without extracting it; the risk is to exert an asymmetrical tearing on the whole assembly when passing over the WiFi chip,
2. Extract the antenna from the receptacle, rotate the antenna 180° and push back the antenna on the receptacle.

Option 1 works quite well (tested by me, but not sure that it does not cause exfoliation of the printed circuit board). Option 2 causes the tearing of the receptacle (what happened to my father) because the anchoring of the receptacle on the printed circuit board is only superficial. Therefore, the required extraction force is bigger than the force that the attachment can support. Please note that we applied the instructions of the Hirose Electric connector manufacturer, consisting to to pull off vertically the U.FL Cable Assembly, in the direction of the connector mating axis (we don't used the extraction tool but but some plastic tweezers):

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

- **We recommend that on the next version, the anchoring of the receptacle on the printed circuit board must be stronger (attached to a anchorage pin inserted in the PCB); some extraction test should be made on the first prototypes.**
- **For the meantime, a warning notice should be present with the product.**

jadonk, 2020-06-09:
Issue migrated to beagleboard/beaglebone-blue#41

Closed 2020-06-09.

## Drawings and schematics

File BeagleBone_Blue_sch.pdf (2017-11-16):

M4

M3

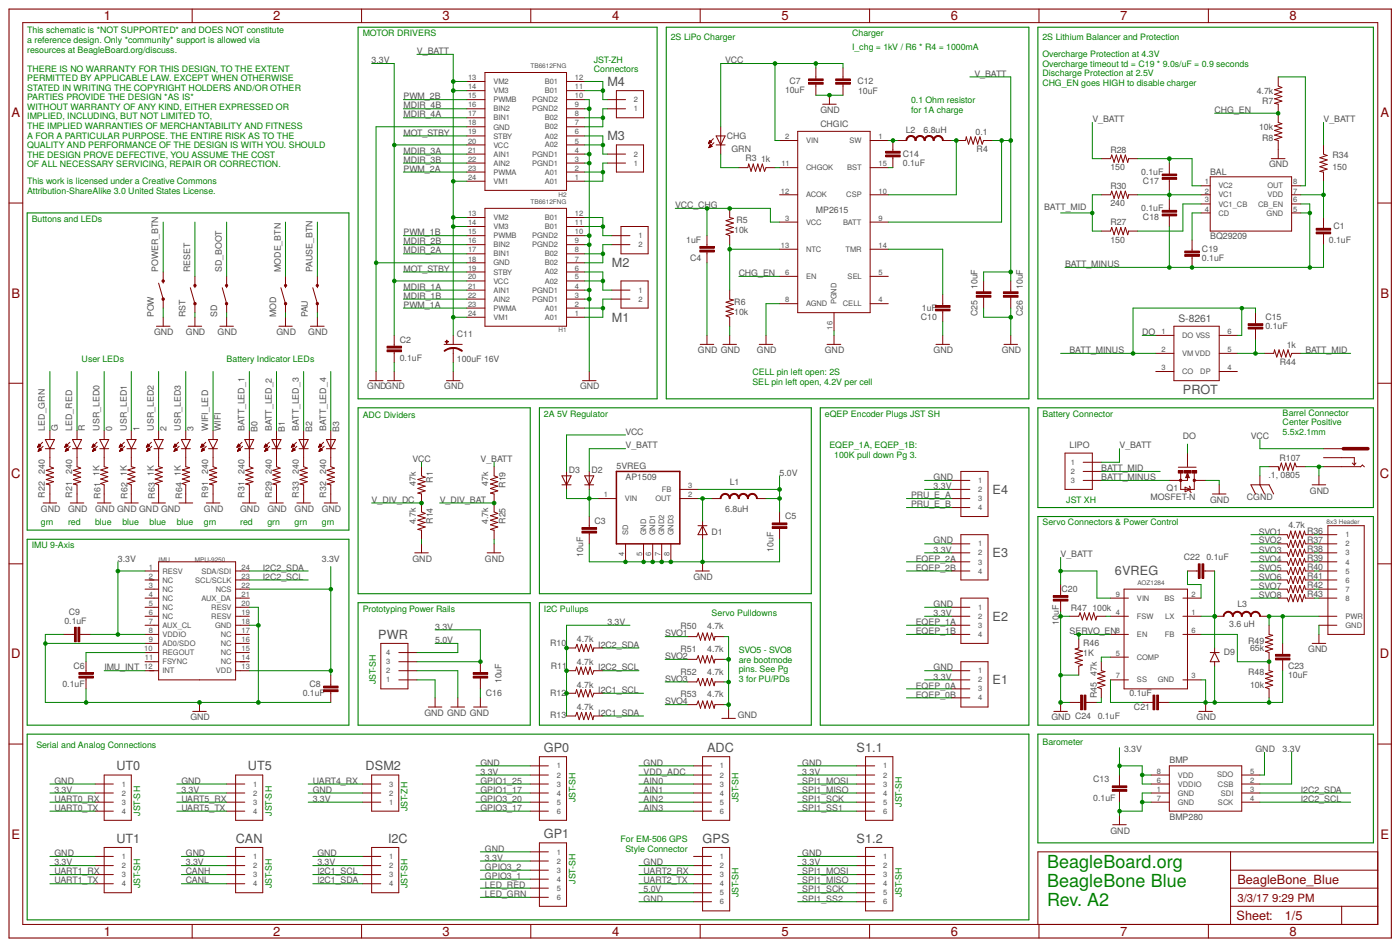
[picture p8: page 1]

This schematic is *NOT SUPPORTED* and DOES NOT constitute
a reference design. Only *community* support is allowed via
resources at BeagleBoard.org/discuss.
THERE IS NO WARRANTY FOR THIS DESIGN, TO THE EXTENT
PERMITTED BY APPLICABLE LAW. EXCEPT WHEN OTHERWISE
STATED IN WRITING THE COPYRIGHT HOLDERS AND/OR OTHER
PARTIES PROVIDE THE DESIGN *AS IS*
WITHOUT WARRANTY OF ANY KIND, EITHER EXPRESSED OR
IMPLIED, INCLUDING, BUT NOT LIMITED TO,
THE IMPLIED WARRANTIES OF MERCHANTABILITY AND FITNESS
A FOR A PARTICULAR PURPOSE. THE ENTIRE RISK AS TO THE
QUALITY AND PERFORMANCE OF THE DESIGN IS WITH YOU. SHOULD
THE DESIGN PROVE DEFECTIVE, YOU ASSUME THE COST
OF ALL NECESSARY SERVICING, REPAIR OR CORRECTION.

2S Lithium Balancer and Protection
Overcharge Protection at 4.3V
Overcharge timeout td = C19 * 9.0s/uF = 0.9 seconds
Discharge Protection at 2.5V
CHG_EN goes HIGH to disable charger

This work is licensed under a Creative Commons
Attribution-ShareAlike 3.0 United States License.

CELL pin left open: 2S
SEL pin left open, 4.2V per cell

eQEP Encoder Plugs JST SH

GND GND
blue blue

Serial and Analog Connections

JST-SH

## SN74LVC1G07_DCK_5

U6

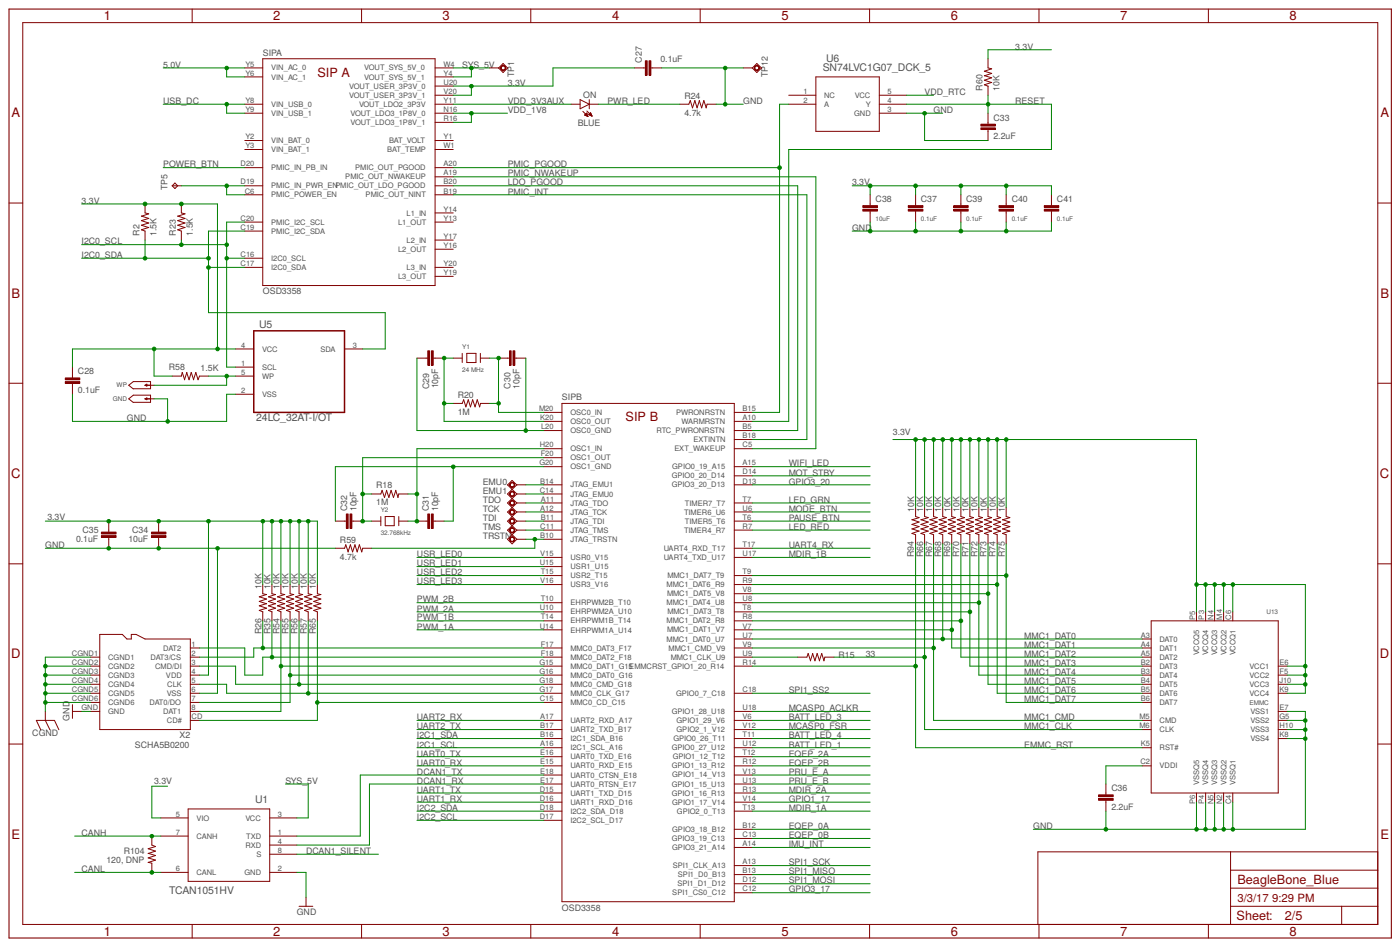
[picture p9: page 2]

OSC1_OUT F20 | WIFI_LED
OSC1_GND G20

R18 Y2 | | JTAG_EMU0 C14 JTAG_EMU1 B14 | MOT_STBY

DCAN1_RX | UART0_RTSN_E17 E17 | PRU_E_B
UART1_TX | UART1_RXD_D16 D16 UART1_TXD_D15 D15 | MDIR_2A

A

A

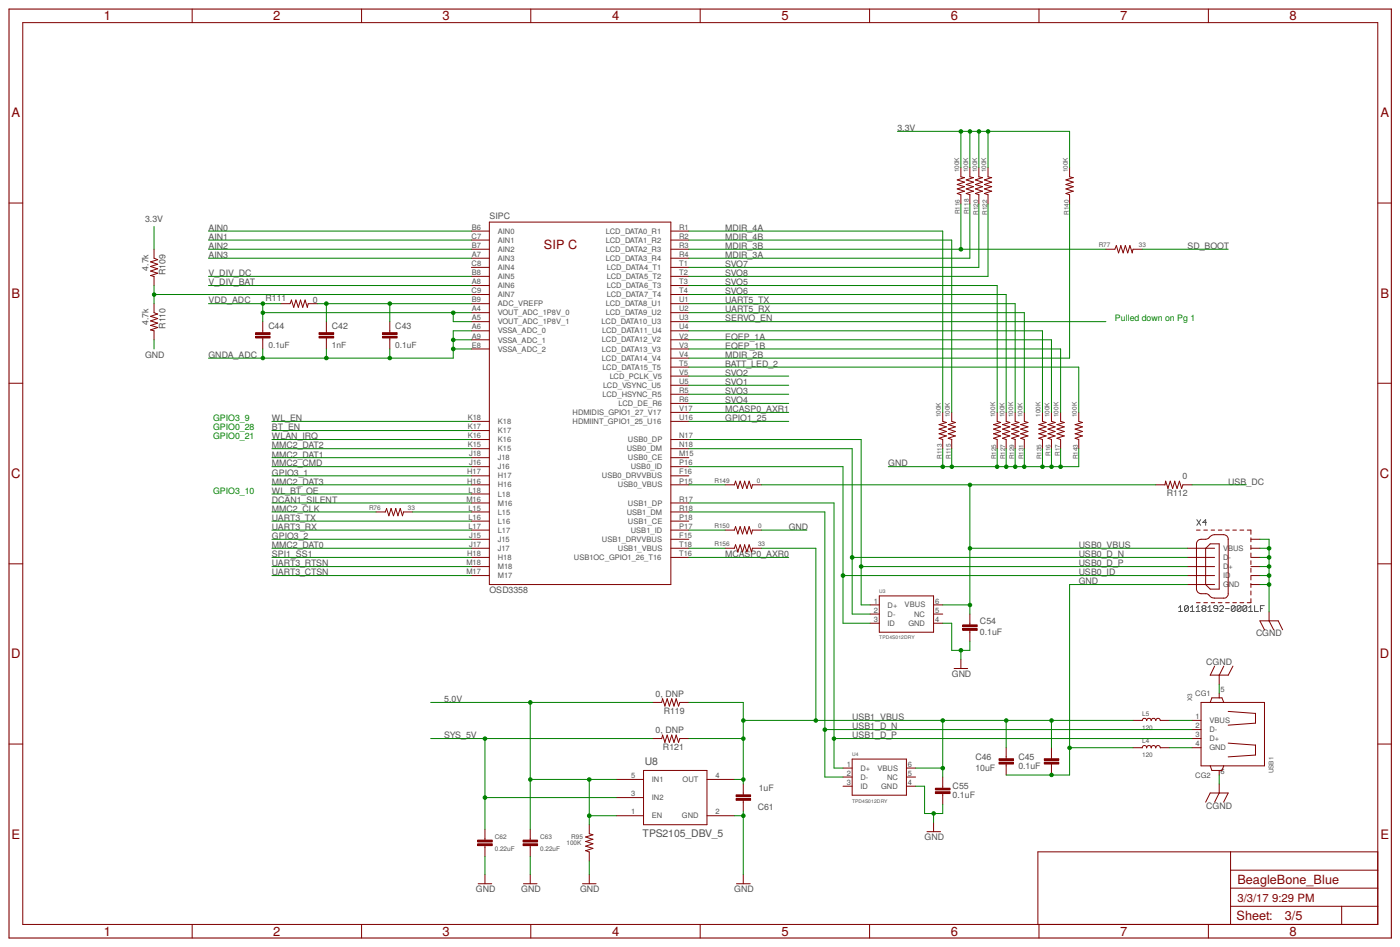
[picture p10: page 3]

MDIR_3B MDIR_3A
SVO7
SVO8
SVO5
SVO6
UART5_RX

R111 0 | ADC_VREFP B9 VOUT_ADC_1P8V_0 A4 | UART5_TX

VOUT_ADC_1P8V_1 A5 | SERVO_EN
VSSA_ADC_1 A9 | EQEP_1A
VSSA_ADC_2 E8 | EQEP_1B
J18 J18 K15 K15 K16 K16 K17 K17 K18 K18 J16 J16 H16 H16 H17 H17 L18 L18 M16 M16 L15 L15 L16 L16 L17 L17 J15 J15 J17 J17 H18 H18 M17 M17 M18 M18 | MDIR_2B

Pulled down on Pg 1

BATT_LED_2

USB0_D_N
USB0_D_P

USB1_D_P

DGND45 | M19 DGND46 | N7 DGND47 | N10 DGND48 | N11 DGND49 | N14 DGND50 | N19 DGND51 | N20 DGND52 | P19 DGND53 | P20 DGND54 | R19 DGND55 | R20 DGND56 | T19 DGND57 | T20 DGND58 | U19 DGND59 | V1 DGND60 | V18 DGND61 | V19 DGND62 | W2 DGND63 | W3

1

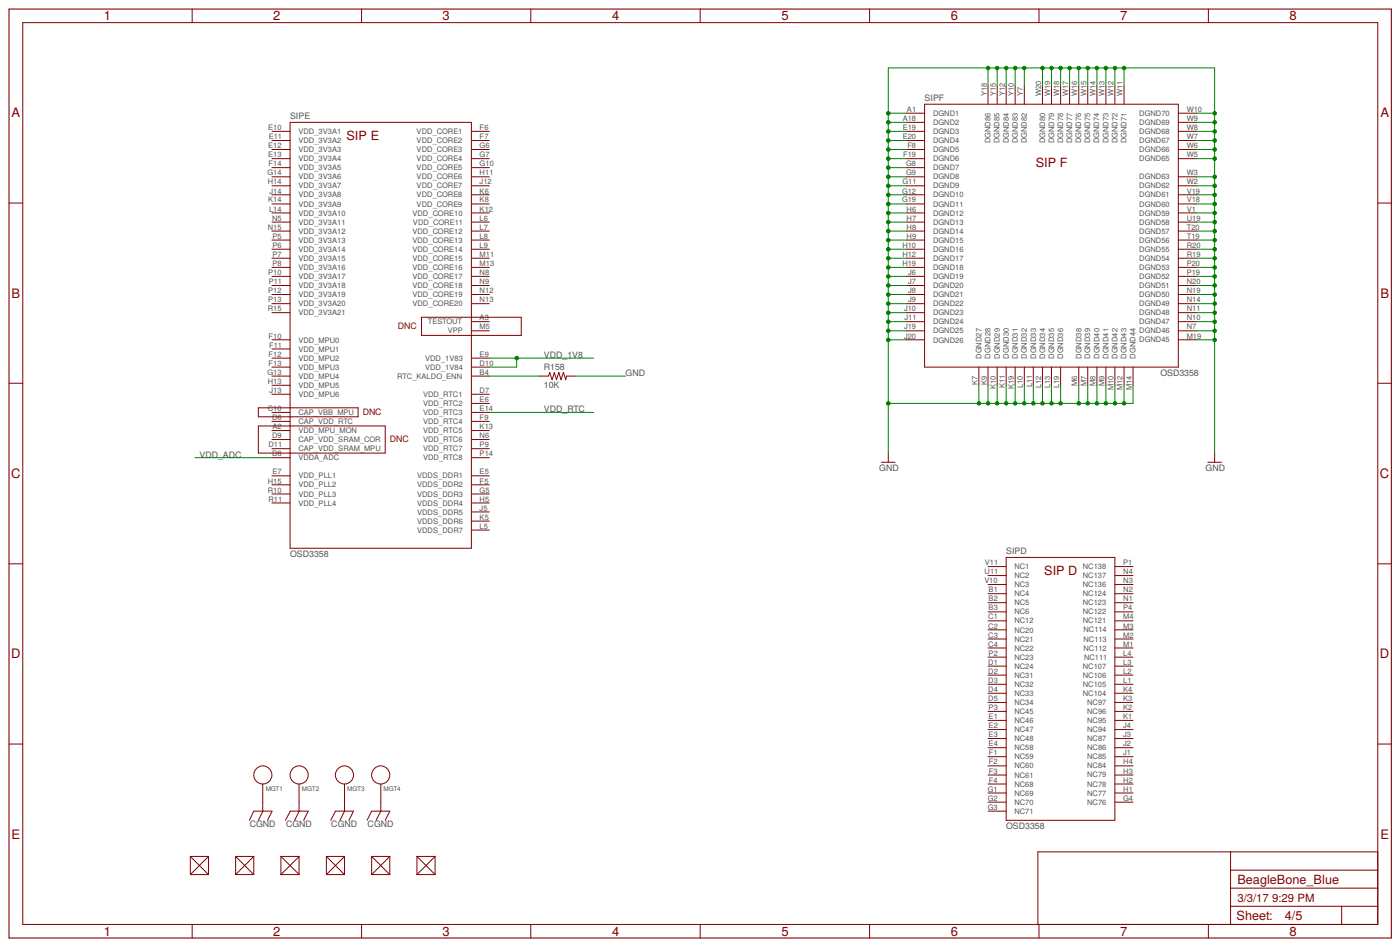
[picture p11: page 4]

A

A

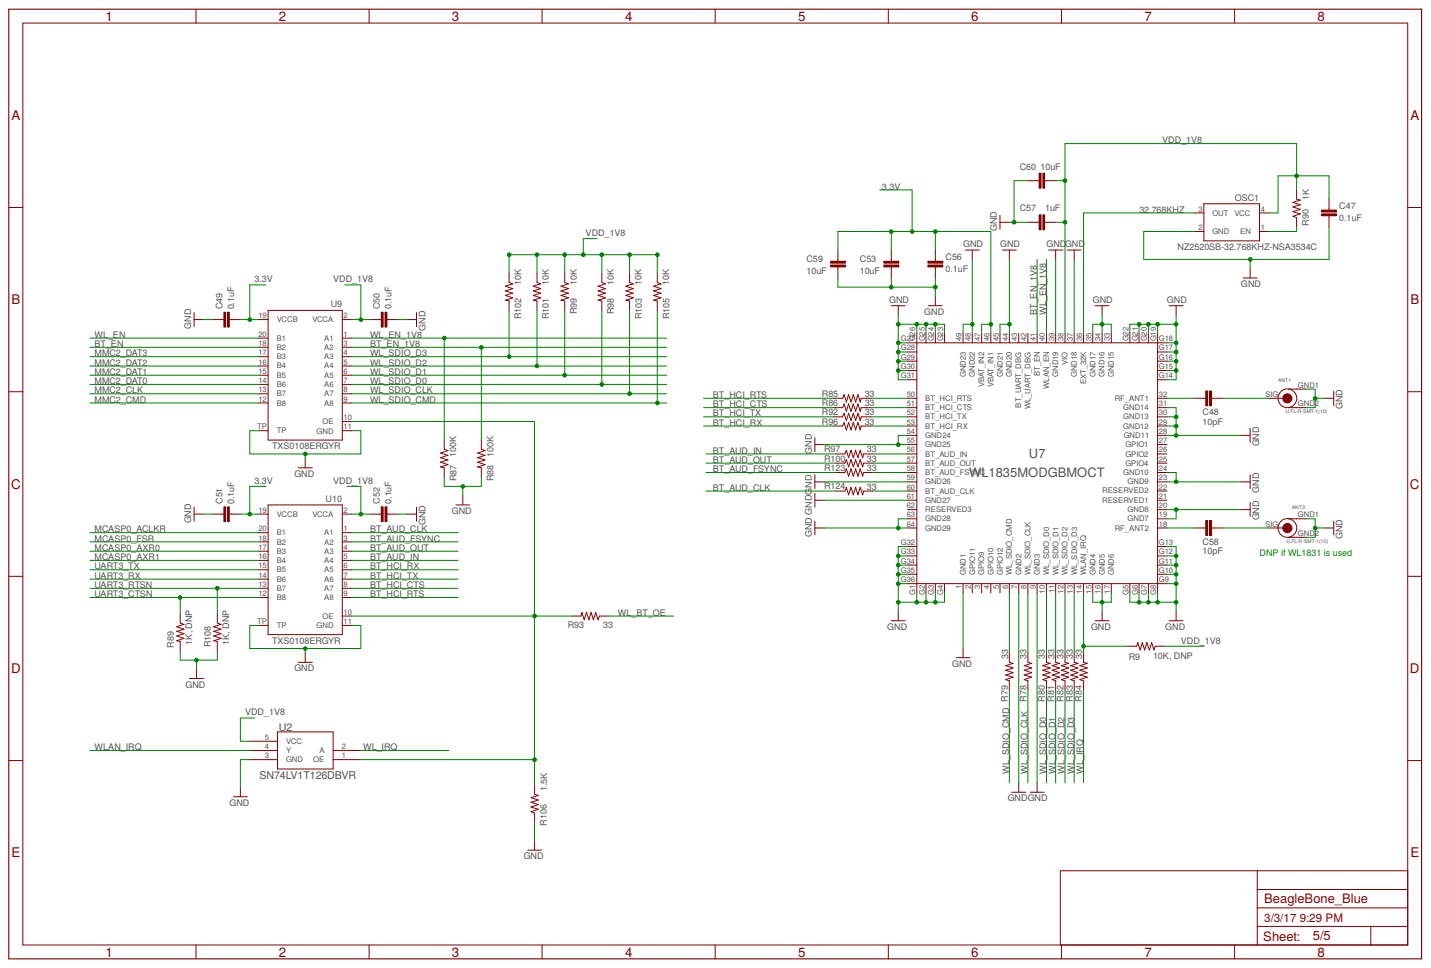
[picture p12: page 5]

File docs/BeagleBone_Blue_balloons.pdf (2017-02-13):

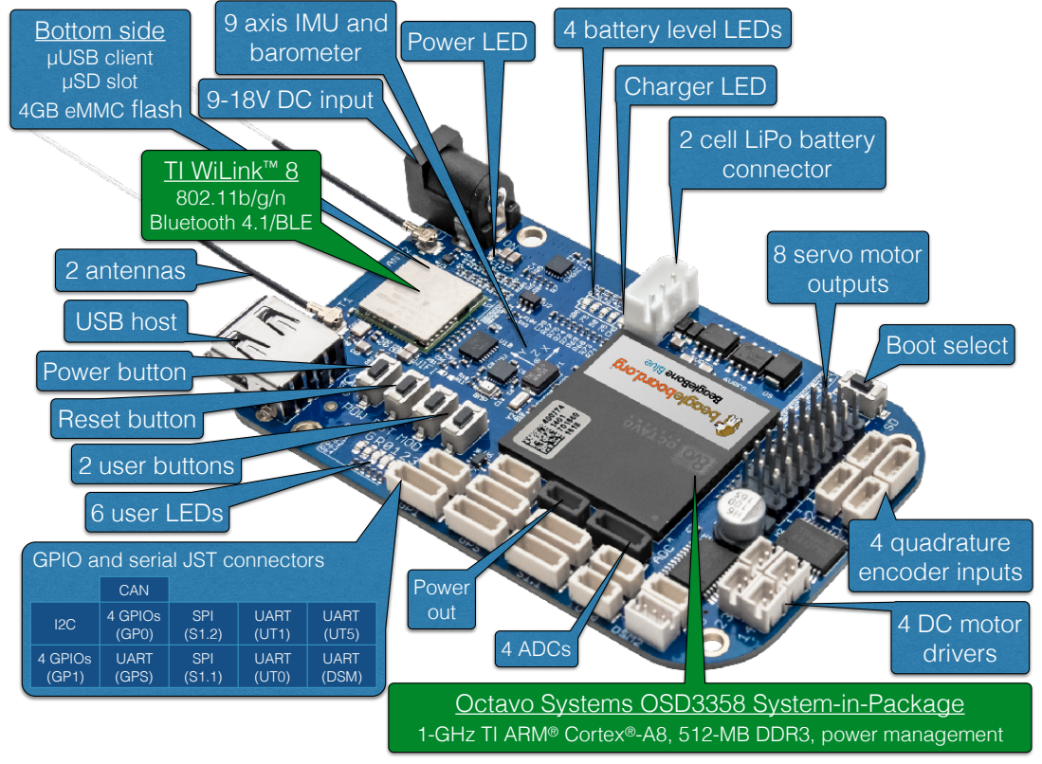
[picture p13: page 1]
8 servo motor outputs; Boot select; 4 DC motor drivers; USB host; Bottom side µUSB client µSD slot 4GB eMMC flash; Power LED; 4 battery level LEDs; Charger LED; Power button; Reset button; 2 user buttons; 6 user LEDs; Power out; 4 ADCs; CAN; 4 quadrature encoder inputs; TI WiLink™ 8 802.11b/g/n Bluetooth 4.1/BLE; 9-18V DC input; 2 antennas

9 axis IMU and
barometer

2 cell LiPo battery
connector

GPIO and serial JST connectors

I2C | 4 GPIOs (GP0) | SPI (S1.2) | UART (UT1) | UART (UT5)

4 GPIOs (GP1) | UART (GPS) | SPI (S1.1) | UART (UT0) | UART (DSM)

Octavo Systems OSD3358 System-in-Package
1-GHz TI ARM® Cortex®-A8, 512-MB DDR3, power management

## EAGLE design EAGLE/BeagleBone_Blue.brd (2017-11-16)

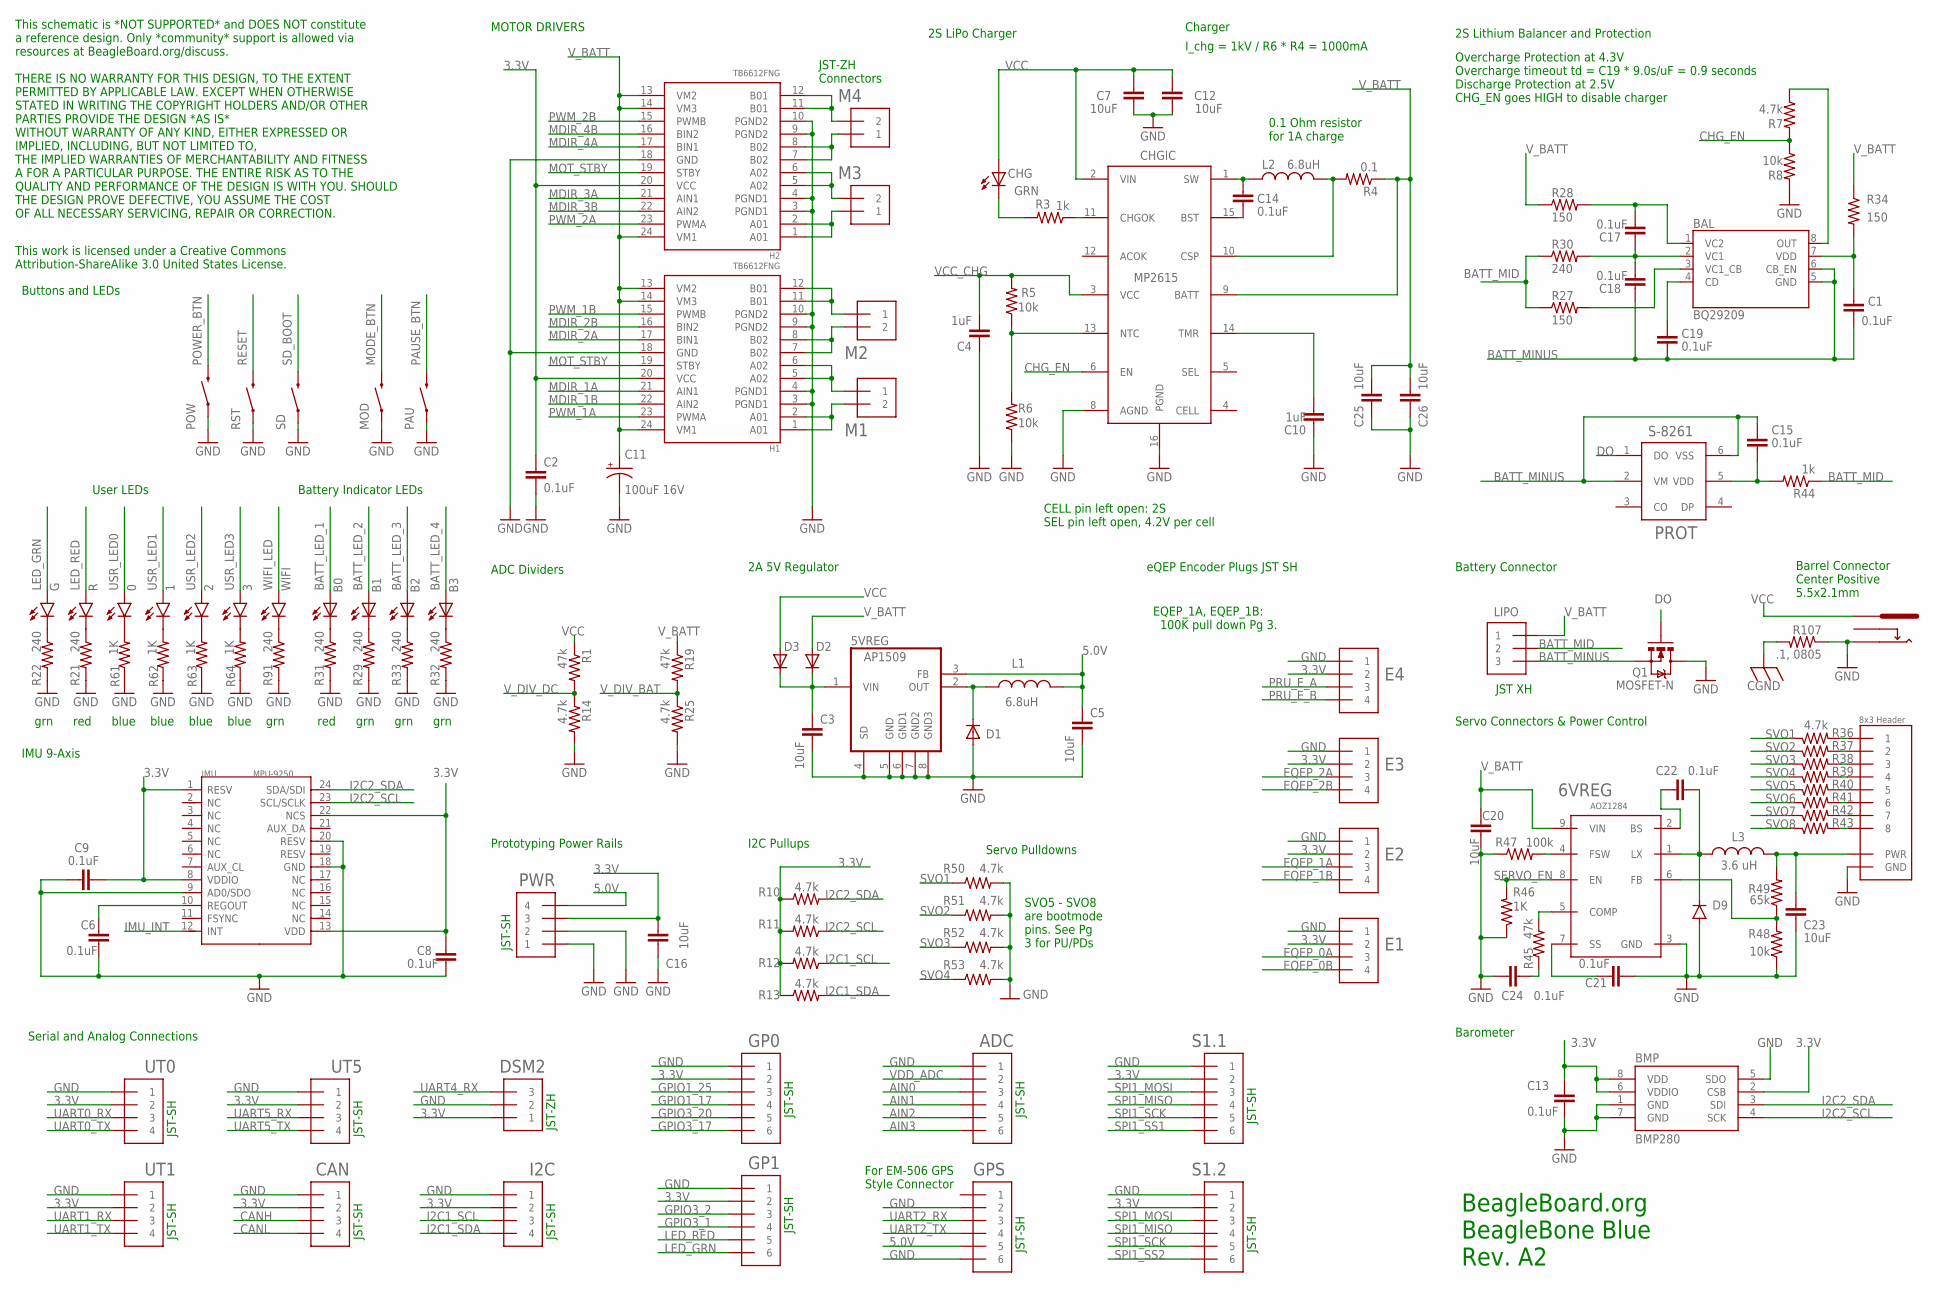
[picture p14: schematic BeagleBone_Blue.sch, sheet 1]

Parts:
0, 1, 2, 3: BLUE; BEAGLEBONE_BLUE_LED-0603
5VREG: AP1509SOIC-8-TIGHT; BEAGLEBONE_BLUE_SO08-TIGHT
6VREG: AOZ1284; SO08-EXPOSED
12V: PJ-102B_POWER_CON
ADC: JST_SH_6
B0: RED; LED-0603
B1, B2, B3: GREEN; LED-0603
BAL: BQ29209; 8-SON_3X3MM
BMP: BMP280
C1, C2, C6, C8, C9, C13, C14, C15, C17, C18, C19, C21, C22, C24: 0.1uF; 0402-CAP
C3, C5, C7, C12, C16, C20, C23, C25, C26: 10uF; 0805
C4, C10: 1uF; 0402-CAP
C11: 100uF 16V; PANASONIC_D
CAN: JST_SH_4; JST_SH_4_SMD
CHG: GRN; LED-0603
CHGIC: MP2615
D1, D2, D3: DIODE_SOD-123FL; ADAFRUIT_SOD-123FL
D9: DIODEDO214AA; DO-214AA
DSM2: JST_ZH_3
E1, E2, E3, E4: JST_SH_4; JST_SH_4_SMD
G: GREEN; BEAGLEBONE_BLUE_LED-0603
GP0, GP1: JST_SH_6
GPS: JST_SH_6
H1, H2: TB6612FNG; SSOP24
I2C: JST_SH_4; JST_SH_4_SMD
IMU: MPU-9250; QFN24G-0.4-3X3MM
J2: STRAWSON_EAGLE_LIB_SERVO_HEADERS_8X; STRAWSON_EAGLE_LIB_3X8_0.1"_HEADER
L1, L2: 6.8uH; SRN6045
L3: 3.6 uH; 8X8MM_INDUCTOR
LIPO: BATTERY; JST_XH_3-PIN
M1, M2, M3, M4: JST_ZH_2
MOD: SWITCH-MOMENTARY-2SMD-1101NE; TACTILE-SWITCH-1101NE
PAU: SWITCH-MOMENTARY-2SMD-1101NE; TACTILE-SWITCH-1101NE
POW: SWITCH-MOMENTARY-2SMD-1101NE; TACTILE-SWITCH-1101NE
PROT: S-8261; SOT-236
PWR: JST_SH_4; JST_SH_4_SMD
Q1: MOSFET-N; SO08-TIGHT
R: RED; BEAGLEBONE_BLUE_LED-0603
R1, R19, R45: 47k; 0402-RES
R3, R44: 1k; 0402-RES
R4: 0.1; 0603-RES
R5, R6, R8, R48: 10k; 0402-RES
R7, R10, R11, R12, R13, R14, R25, R36, R37, R38, R39, R40, R41, R42, R43, R50, R51, R52, R53: 4.7k; 0402-RES
R21, R22, R29, R30, R31, R32, R33, R91: 240; 0402-RES
R27, R28, R34: 150; 0402-RES
R46, R61, R62, R63, R64: 1K; 0402-RES
R47: 100k; 0402-RES
R49: 65k; 0402-RES
R107: .1, 0805; R0805
RST: SWITCH-MOMENTARY-2SMD-1101NE; TACTILE-SWITCH-1101NE
S1.1, S1.2: JST_SH_6
SD: SWITCH-MOMENTARY-2SMD-1101NE; TACTILE-SWITCH-1101NE
UT0, UT1, UT5: JST_SH_4; JST_SH_4_SMD
WIFI: GREEN; BEAGLEBONE_BLUE_LED-0603

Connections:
3.3V: BMP.2 (CSB), BMP.6 (VDDIO), BMP.8 (VDD), C2.2, C8.1, C9.2, C13.1, C16.1, CAN.2, DSM2.P$1 (1), E1.2, E2.2, E3.2, E4.2, GP0.2, GP1.2, H1.20 (VCC), H2.20 (VCC), I2C.2, IMU.1 (RESV), IMU.8 (VDDIO), IMU.13 (VDD), IMU.22 (NCS), PWR.3, R10.1, R11.2, R12.2, R13.1, S1.1.2, S1.2.2, UT0.2, UT1.2, UT5.2; also elsewhere on the board
5.0V: 5VREG.3 (FB), C5.1, GPS.5, L1.2, PWR.4; also elsewhere on the board
AIN0: ADC.3; also elsewhere on the board
AIN1: ADC.4; also elsewhere on the board
AIN2: ADC.5; also elsewhere on the board
AIN3: ADC.6; also elsewhere on the board
BATT_LED_1: B0.A; also elsewhere on the board
BATT_LED_2: B1.A; also elsewhere on the board
BATT_LED_3: B2.A; also elsewhere on the board
BATT_LED_4: B3.A; also elsewhere on the board
BATT_MID: LIPO.P$2 (2), R27.1, R30.1, R44.1
BATT_MINUS: BAL.5 (GND), BAL.6 (CB_EN), C1.2, C15.1, C18.1, C19.2, LIPO.P$3 (3), PROT.2 (VM), PROT.6 (VSS), Q1.1 (S), Q1.2 (S), Q1.3 (S)
CANH: CAN.3; also elsewhere on the board
CANL: CAN.4; also elsewhere on the board
CGND: R107.2; also elsewhere on the board
CHG_EN: CHGIC.6 (EN), R7.2, R8.1
CO: BAL.8 (OUT), R7.1
DO: PROT.1 (DO), Q1.4 (G)
EQEP_0A: E1.3; also elsewhere on the board
EQEP_0B: E1.4; also elsewhere on the board
EQEP_1A: E2.3; also elsewhere on the board
EQEP_1B: E2.4; also elsewhere on the board
EQEP_2A: E3.3; also elsewhere on the board
EQEP_2B: E3.4; also elsewhere on the board
GND: 5VREG.4 (SD), 5VREG.5 (GND), 5VREG.6 (GND1), 5VREG.7 (GND2), 5VREG.8 (GND3), 6VREG.3 (GND), 12V.OUT, ADC.1, BMP.1 (GND), BMP.5 (SDO), BMP.7 (GND), C2.1, C3.2, C4.1, C5.2, C6.2, C7.2, C8.2, C9.1, C10.1, C11.-, C12.2, C13.2, C16.2, C20.1, C21.1, C23.1, C24.1, C25.2, C26.2, CAN.1, CHGIC.8 (AGND), CHGIC.16 (PGND), D1.A, D9.A, DSM2.P$2 (2), E1.1, E2.1, E3.1, E4.1, GP0.1, GP1.1, GPS.2, GPS.6, H1.3 (PGND1), H1.4 (PGND1), H1.9 (PGND2), H1.10 (PGND2), H1.18 (GND), H2.3 (PGND1), H2.4 (PGND1), H2.9 (PGND2), H2.10 (PGND2), H2.18 (GND), I2C.1, IMU.9 (AD0/SDO), IMU.18 (GND), IMU.20 (RESV), J2.P$13 (GND), J2.P$14 (GND), J2.P$15 (GND), J2.P$16 (GND), J2.P$17 (GND), J2.P$18 (GND), J2.P$23 (GND), J2.P$24 (GND), MOD.1, PAU.1, POW.1, PWR.1, PWR.2, Q1.5 (D), Q1.6 (D), Q1.7 (D), Q1.8 (D), R6.1, R8.2, R14.2, R21.2, R22.2, R25.2, R29.2, R31.2, R32.2, R33.2, R46.1, R47.1, R48.1, R50.2, R51.2, R52.2, R53.2, R61.1, R62.1, R63.1, R64.1, R91.2, R107.1, RST.1, S1.1.1, S1.2.1, SD.1, UT0.1, UT1.1, UT5.1; also elsewhere on the board
GPIO1_17: GP0.4; also elsewhere on the board
GPIO1_25: GP0.3; also elsewhere on the board
GPIO3_1: GP1.4; also elsewhere on the board
GPIO3_2: GP1.3; also elsewhere on the board
GPIO3_17: GP0.6; also elsewhere on the board
GPIO3_20: GP0.5; also elsewhere on the board
I2C1_SCL: I2C.3, R12.1; also elsewhere on the board
I2C1_SDA: I2C.4, R13.2; also elsewhere on the board
I2C2_SCL: BMP.4 (SCK), IMU.23 (SCL/SCLK), R11.1; also elsewhere on the board
I2C2_SDA: BMP.3 (SDI), IMU.24 (SDA/SDI), R10.2; also elsewhere on the board
IMU_INT: IMU.12 (INT); also elsewhere on the board
L3: B2.C, R33.1
L4: B3.C, R32.1
LED_GRN: G.A, GP1.6; also elsewhere on the board
LED_RED: GP1.5, R.A; also elsewhere on the board
MDIR_1A: H1.21 (AIN1); also elsewhere on the board
MDIR_1B: H1.22 (AIN2); also elsewhere on the board
MDIR_2A: H1.17 (BIN1); also elsewhere on the board
MDIR_2B: H1.16 (BIN2); also elsewhere on the board
MDIR_3A: H2.21 (AIN1); also elsewhere on the board
MDIR_3B: H2.22 (AIN2); also elsewhere on the board
MDIR_4A: H2.17 (BIN1); also elsewhere on the board
MDIR_4B: H2.16 (BIN2); also elsewhere on the board
MODE_BTN: MOD.2; also elsewhere on the board
MOT1A: H1.1 (A01), H1.2 (A01), M1.P$2 (2)
MOT1B: H1.5 (A02), H1.6 (A02), M1.P$1 (1)
MOT2A: H1.11 (B01), H1.12 (B01), M2.P$1 (1)
MOT2B: H1.7 (B02), H1.8 (B02), M2.P$2 (2)
MOT3A: H2.1 (A01), H2.2 (A01), M3.P$1 (1)
MOT3B: H2.5 (A02), H2.6 (A02), M3.P$2 (2)
MOT4A: H2.11 (B01), H2.12 (B01), M4.P$2 (2)
MOT4B: H2.7 (B02), H2.8 (B02), M4.P$1 (1)
MOT_STBY: H1.19 (STBY), H2.19 (STBY); also elsewhere on the board
unnamed: J2.P$1 (1), R36.2
unnamed: G.C, R22.1
unnamed: BAL.2 (VC1), C17.1, C18.2, R30.2
unnamed: R.C, R21.1
unnamed: BAL.1 (VC2), C17.2, R28.2
unnamed: 6VREG.7 (SS), C21.2
unnamed: C15.2, PROT.5 (VDD), R44.2
unnamed: C6.1, IMU.10 (REGOUT)
unnamed: C14.1, CHGIC.15 (BST)
unnamed: 5VREG.2 (OUT), D1.C, L1.1
unnamed: CHG.C, R3.2
unnamed: CHGIC.11 (CHGOK), R3.1
unnamed: R91.1, WIFI.C
unnamed: BAL.4 (CD), C19.1
unnamed: J2.P$2 (2), R37.2
unnamed: BAL.7 (VDD), C1.1, R34.2
unnamed: J2.P$3 (3), R38.2
unnamed: J2.P$4 (4), R39.2
unnamed: 0.C, R61.2
unnamed: B1.C, R29.1
unnamed: B0.C, R31.1
unnamed: BAL.3 (VC1_CB), R27.2
unnamed: J2.P$5 (5), R40.2
unnamed: J2.P$6 (6), R41.2
unnamed: 6VREG.2 (BS), C22.1
unnamed: J2.P$19 (7), R42.2
unnamed: C14.2, CHGIC.1 (SW), L2.1
unnamed: J2.P$20 (8), R43.2
unnamed: 1.C, R62.2
unnamed: 2.C, R63.2
unnamed: 3.C, R64.2
unnamed: 6VREG.1 (LX), C22.2, D9.C, L3.1
unnamed: 6VREG.4 (FSW), R47.2
unnamed: C23.2, J2.P$7 (PWR), J2.P$8 (PWR), J2.P$9 (PWR), J2.P$10 (PWR), J2.P$11 (PWR), J2.P$12 (PWR), J2.P$21 (PWR), J2.P$22 (PWR), L3.2, R49.2
unnamed: 6VREG.5 (COMP), R45.2
unnamed: 6VREG.6 (FB), R48.2, R49.1
unnamed: C24.2, R45.1
unnamed: CHGIC.10 (CSP), L2.2, R4.2
unnamed: C10.2, CHGIC.14 (TMR)
unnamed: CHGIC.13 (NTC), R5.1, R6.2
unnamed: 5VREG.1 (VIN), C3.1, D2.C, D3.C
PAUSE_BTN: PAU.2; also elsewhere on the board
POWER_BTN: POW.2; also elsewhere on the board
PRU_E_A: E4.3; also elsewhere on the board
PRU_E_B: E4.4; also elsewhere on the board
PWM_1A: H1.23 (PWMA); also elsewhere on the board
PWM_1B: H1.15 (PWMB); also elsewhere on the board
PWM_2A: H2.23 (PWMA); also elsewhere on the board
PWM_2B: H2.15 (PWMB); also elsewhere on the board
RESET: RST.2; also elsewhere on the board
SD_BOOT: SD.2; also elsewhere on the board
SERVO_EN: 6VREG.8 (EN), R46.2; also elsewhere on the board
SPI1_MISO: S1.1.4, S1.2.4; also elsewhere on the board
SPI1_MOSI: S1.1.3, S1.2.3; also elsewhere on the board
SPI1_SCK: S1.1.5, S1.2.5; also elsewhere on the board
SPI1_SS1: S1.1.6; also elsewhere on the board
SPI1_SS2: S1.2.6; also elsewhere on the board
SVO1: R36.1, R50.1; also elsewhere on the board
SVO2: R37.1, R51.1; also elsewhere on the board
SVO3: R38.1, R52.1; also elsewhere on the board
SVO4: R39.1, R53.1; also elsewhere on the board
SVO5: R40.1; also elsewhere on the board
SVO6: R41.1; also elsewhere on the board
SVO7: R42.1; also elsewhere on the board
SVO8: R43.1; also elsewhere on the board
UART0_RX: UT0.3; also elsewhere on the board
UART0_TX: UT0.4; also elsewhere on the board
UART1_RX: UT1.3; also elsewhere on the board
UART1_TX: UT1.4; also elsewhere on the board
UART2_RX: GPS.3; also elsewhere on the board
UART2_TX: GPS.4; also elsewhere on the board
UART4_RX: DSM2.P$3 (3); also elsewhere on the board
UART5_RX: UT5.3; also elsewhere on the board
UART5_TX: UT5.4; also elsewhere on the board
USR_LED0: 0.A; also elsewhere on the board
USR_LED1: 1.A; also elsewhere on the board
USR_LED2: 2.A; also elsewhere on the board
USR_LED3: 3.A; also elsewhere on the board
VCC: 12V.IN, C7.1, C12.1, CHG.A, CHGIC.2 (VIN), D3.A, R1.1
VCC_CHG: C4.2, CHGIC.3 (VCC), R5.2
VDD_ADC: ADC.2; also elsewhere on the board
V_BATT: 6VREG.9 (VIN), C11.+, C20.2, C25.1, C26.1, CHGIC.9 (BATT), D2.A, H1.13 (VM2), H1.14 (VM3), H1.24 (VM1), H2.13 (VM2), H2.14 (VM3), H2.24 (VM1), LIPO.P$1 (1), R4.1, R19.1, R28.1, R34.1
V_DIV_BAT: R19.2, R25.1; also elsewhere on the board
V_DIV_DC: R1.2, R14.1; also elsewhere on the board
WIFI_LED: WIFI.A; also elsewhere on the board

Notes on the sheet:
BeagleBoard.org BeagleBone Blue Rev. A2
Barrel Connector Center Positive 5.5x2.1mm
ADC Dividers
Prototyping Power Rails
Buttons and LEDs
eQEP Encoder Plugs JST SH
I2C Pullups
2A 5V Regulator
Overcharge Protection at 4.3V Overcharge timeout td = C19 * 9.0s/uF = 0.9 seconds Discharge Protection at 2.5V CHG_EN goes HIGH to disable charger
I_chg = 1kV / R6 * R4 = 1000mA
Battery Indicator LEDs
MOTOR DRIVERS
Servo Connectors & Power Control
JST-ZH
Barometer
Charger
JST-ZH Connectors
IMU 9-Axis
For EM-506 GPS Style Connector
2S Lithium Balancer and Protection
red
grn
JST XH
Battery Connector
JST-SH
Serial and Analog Connections
Servo Pulldowns
2S LiPo Charger
0.1 Ohm resistor for 1A charge
CELL pin left open: 2S SEL pin left open, 4.2V per cell
This schematic is *NOT SUPPORTED* and DOES NOT constitute a reference design. Only *community* support is allowed via resources at BeagleBoard.org/discuss. THERE IS NO WARRANTY FOR THIS DESIGN, TO THE EXTENT PERMITTED BY APPLICABLE LAW. EXCEPT WHEN OTHERWISE STATED IN WRITING THE COPYRIGHT HOLDERS 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
This work is licensed under a Creative Commons Attribution-ShareAlike 3.0 United States License.
User LEDs
blue
EQEP_1A, EQEP_1B: 100K pull down Pg 3.
SVO5 - SVO8 are bootmode pins. See Pg 3 for PU/PDs

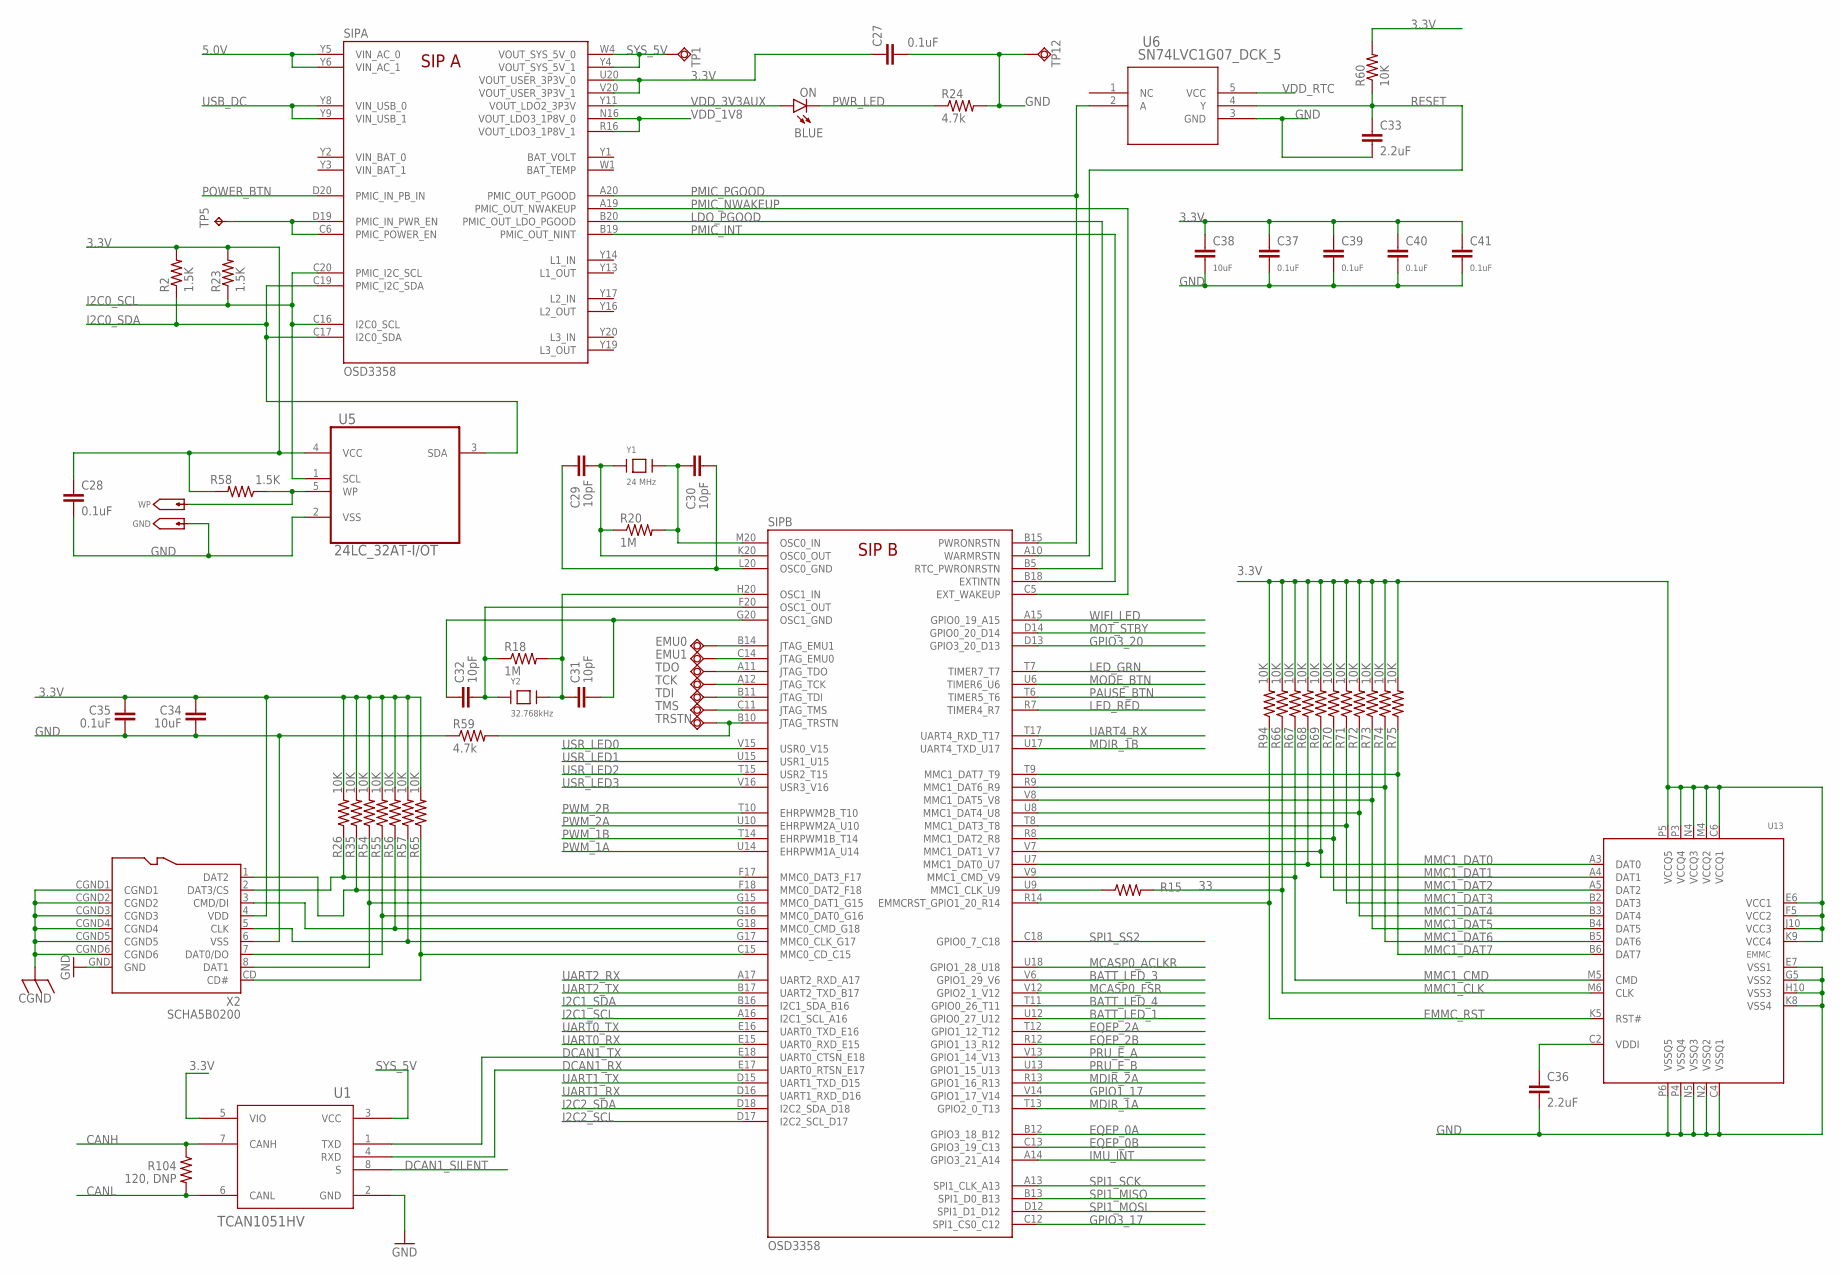
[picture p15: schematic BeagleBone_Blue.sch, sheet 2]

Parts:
C27, C28, C35, C37, C39, C40, C41: 0.1uF; 0402-CAP
C29, C30, C31, C32: 10pF; 0402-CAP
C33, C36: 2.2uF; 0402-CAP
C34, C38: 10uF; 0805
EMU0, EMU1: TPSQB1,27; B1,27
GND: GHI2_TESTPAD/W_HOLE_1X1
ON: BLUE; BEAGLEBONE_BLUE_LED-0603
R2, R23, R58: 1.5K; 0402-RES
R15: 33; 0402-RES
R18, R20: 1M; 0402-RES
R24, R59: 4.7k; 0402-RES
R26, R35, R54, R55, R56, R57, R60, R65, R66, R67, R68, R69, R70, R71, R72, R73, R74, R75, R94: 10K; 0402-RES
R104: 120, DNP; 0603-RES
SIP: OSD3358; BEAGLEBONE_BLUE_OSD3358
TCK: TPSQB1,27; B1,27
TDI: TPSQB1,27; B1,27
TDO: TPSQB1,27; B1,27
TMS: TPSQB1,27; B1,27
TP1, TP12: TPSQB1,27; B1,27
TP5: TPB0,65; BEAGLEBONE_BLUE_B0,65
TRSTN: TPSQB1,27; B1,27
U1: TCAN1051HV; BEAGLEBONE_BLUE_D8
U5: 24LC_32AT-I/OT; SOT95P290X145-5N
U6: SN74LVC1G07_DCK_5; BEAGLEBONE_BLUE_DCK5
U13: EMMC; MICRON_EMMC_153
WP: GHI2_TESTPAD/W_HOLE_1X1
X2: SCHA5B0200
Y1: 24 MHz; CRYSTAL_5X3.2MM
Y2: 32.768kHz; CRYSTAL_3.2X1.5

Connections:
3.3V: C27.1, C28.1, C34.2, C35.2, C37.1, C38.1, C39.1, C40.1, C41.1, R2.2, R23.2, R26.2, R35.2, R54.2, R55.2, R56.2, R57.2, R58.2, R60.2, R65.2, R66.2, R67.2, R68.2, R69.2, R70.2, R71.2, R72.2, R73.2, R74.2, R75.2, R94.2, SIP.U20 (VOUT_USER_3P3V_0), SIP.V20 (VOUT_USER_3P3V_1), U1.5 (VIO), U5.4 (VCC), U13.C6 (VCCQ1), U13.E6 (VCC1), U13.F5 (VCC2), U13.J10 (VCC3), U13.K9 (VCC4), U13.M4 (VCCQ2), U13.N4 (VCCQ3), U13.P3 (VCCQ4), U13.P5 (VCCQ5), X2.4 (VDD); also elsewhere on the board
5.0V: SIP.Y5 (VIN_AC_0), SIP.Y6 (VIN_AC_1); also elsewhere on the board
BATT_LED_1: SIP.U12 (GPIO0_27_U12); also elsewhere on the board
BATT_LED_3: SIP.V6 (GPIO1_29_V6); also elsewhere on the board
BATT_LED_4: SIP.T11 (GPIO0_26_T11); also elsewhere on the board
CANH: R104.1, U1.7 (CANH); also elsewhere on the board
CANL: R104.2, U1.6 (CANL); also elsewhere on the board
CGND: X2.CGND1, X2.CGND2, X2.CGND3, X2.CGND4, X2.CGND5, X2.CGND6; also elsewhere on the board
DCAN1_RX: SIP.E17 (UART0_RTSN_E17), U1.4 (RXD)
DCAN1_SILENT: U1.8 (S); also elsewhere on the board
DCAN1_TX: SIP.E18 (UART0_CTSN_E18), U1.1 (TXD)
EMMC_RST: R94.1, SIP.R14 (EMMCRST_GPIO1_20_R14), U13.K5 (RST#)
EQEP_0A: SIP.B12 (GPIO3_18_B12); also elsewhere on the board
EQEP_0B: SIP.C13 (GPIO3_19_C13); also elsewhere on the board
EQEP_2A: SIP.T12 (GPIO1_12_T12); also elsewhere on the board
EQEP_2B: SIP.R12 (GPIO1_13_R12); also elsewhere on the board
GND: C27.2, C28.2, C33.2, C34.1, C35.1, C36.2, C37.2, C38.2, C39.2, C40.2, C41.2, GND.P$1, R24.2, R59.1, TP12.TP, U1.2 (GND), U5.2 (VSS), U6.3 (GND), U13.C4 (VSSQ1), U13.E7 (VSS1), U13.G5 (VSS2), U13.H10 (VSS3), U13.K8 (VSS4), U13.N2 (VSSQ2), U13.N5 (VSSQ3), U13.P4 (VSSQ4), U13.P6 (VSSQ5), X2.6 (VSS), X2.GND; also elsewhere on the board
GPIO1_17: SIP.V14 (GPIO1_17_V14); also elsewhere on the board
GPIO3_17: SIP.C12 (SPI1_CS0_C12); also elsewhere on the board
GPIO3_20: SIP.D13 (GPIO3_20_D13); also elsewhere on the board
I2C0_SCL: R23.1, SIP.C16 (I2C0_SCL), SIP.C20 (PMIC_I2C_SCL), U5.1 (SCL)
I2C0_SDA: R2.1, SIP.C17 (I2C0_SDA), SIP.C19 (PMIC_I2C_SDA), U5.3 (SDA)
I2C1_SCL: SIP.A16 (I2C1_SCL_A16); also elsewhere on the board
I2C1_SDA: SIP.B16 (I2C1_SDA_B16); also elsewhere on the board
I2C2_SCL: SIP.D17 (I2C2_SCL_D17); also elsewhere on the board
I2C2_SDA: SIP.D18 (I2C2_SDA_D18); also elsewhere on the board
IMU_INT: SIP.A14 (GPIO3_21_A14); also elsewhere on the board
LDO_PGOOD: SIP.B5 (RTC_PWRONRSTN), SIP.B20 (PMIC_OUT_LDO_PGOOD)
LED_GRN: SIP.T7 (TIMER7_T7); also elsewhere on the board
LED_RED: SIP.R7 (TIMER4_R7); also elsewhere on the board
MCASP0_ACLKR: SIP.U18 (GPIO1_28_U18); also elsewhere on the board
MCASP0_FSR: SIP.V12 (GPIO2_1_V12); also elsewhere on the board
MDIR_1A: SIP.T13 (GPIO2_0_T13); also elsewhere on the board
MDIR_1B: SIP.U17 (UART4_TXD_U17); also elsewhere on the board
MDIR_2A: SIP.R13 (GPIO1_16_R13); also elsewhere on the board
MMC1_CLK: R15.2, R66.1, U13.M6 (CLK)
MMC1_CMD: R67.1, SIP.V9 (MMC1_CMD_V9), U13.M5 (CMD)
MMC1_DAT0: R68.1, SIP.U7 (MMC1_DAT0_U7), U13.A3 (DAT0)
MMC1_DAT1: R69.1, SIP.V7 (MMC1_DAT1_V7), U13.A4 (DAT1)
MMC1_DAT2: R70.1, SIP.R8 (MMC1_DAT2_R8), U13.A5 (DAT2)
MMC1_DAT3: R71.1, SIP.T8 (MMC1_DAT3_T8), U13.B2 (DAT3)
MMC1_DAT4: R72.1, SIP.U8 (MMC1_DAT4_U8), U13.B3 (DAT4)
MMC1_DAT5: R73.1, SIP.V8 (MMC1_DAT5_V8), U13.B4 (DAT5)
MMC1_DAT6: R74.1, SIP.R9 (MMC1_DAT6_R9), U13.B5 (DAT6)
MMC1_DAT7: R75.1, SIP.T9 (MMC1_DAT7_T9), U13.B6 (DAT7)
MODE_BTN: SIP.U6 (TIMER6_U6); also elsewhere on the board
MOT_STBY: SIP.D14 (GPIO0_20_D14); also elsewhere on the board
unnamed: R57.1, SIP.G17 (MMC0_CLK_G17), X2.5 (CLK)
unnamed: R26.1, SIP.F17 (MMC0_DAT3_F17), X2.2 (DAT3/CS)
unnamed: SIP.C6 (PMIC_POWER_EN), SIP.D19 (PMIC_IN_PWR_EN), TP5.TP
unnamed: C30.1, R20.2, SIP.M20 (OSC0_IN), Y1.2
unnamed: C29.1, R20.1, SIP.K20 (OSC0_OUT), Y1.1
unnamed: R58.1, U5.5 (WP), WP.P$1
unnamed: C29.2, C30.2, SIP.L20 (OSC0_GND)
unnamed: C31.1, R18.2, SIP.H20 (OSC1_IN), Y2.P$2
unnamed: C32.2, R18.1, SIP.F20 (OSC1_OUT), Y2.P$1
unnamed: C31.2, C32.1, SIP.G20 (OSC1_GND)
unnamed: EMU0.TP, SIP.B14 (JTAG_EMU1)
unnamed: EMU1.TP, SIP.C14 (JTAG_EMU0)
unnamed: SIP.A11 (JTAG_TDO), TDO.TP
unnamed: SIP.A12 (JTAG_TCK), TCK.TP
unnamed: SIP.B11 (JTAG_TDI), TDI.TP
unnamed: SIP.C11 (JTAG_TMS), TMS.TP
unnamed: R59.2, SIP.B10 (JTAG_TRSTN), TRSTN.TP
unnamed: R54.1, SIP.G15 (MMC0_DAT1_G15), X2.8 (DAT1)
unnamed: R56.1, SIP.G18 (MMC0_CMD_G18), X2.3 (CMD/DI)
unnamed: R65.1, SIP.C15 (MMC0_CD_C15), X2.CD (CD#)
unnamed: R55.1, SIP.G16 (MMC0_DAT0_G16), X2.7 (DAT0/DO)
unnamed: C36.1, U13.C2 (VDDI)
unnamed: R15.1, SIP.U9 (MMC1_CLK_U9)
NTE: R35.1, SIP.F18 (MMC0_DAT2_F18), X2.1 (DAT2)
PAUSE_BTN: SIP.T6 (TIMER5_T6); also elsewhere on the board
PMIC_INT: SIP.B18 (EXTINTN), SIP.B19 (PMIC_OUT_NINT)
PMIC_NWAKEUP: SIP.A19 (PMIC_OUT_NWAKEUP), SIP.C5 (EXT_WAKEUP)
PMIC_PGOOD: SIP.A20 (PMIC_OUT_PGOOD), SIP.B15 (PWRONRSTN), U6.2 (A)
POWER_BTN: SIP.D20 (PMIC_IN_PB_IN); also elsewhere on the board
PRU_E_A: SIP.V13 (GPIO1_14_V13); also elsewhere on the board
PRU_E_B: SIP.U13 (GPIO1_15_U13); also elsewhere on the board
PWM_1A: SIP.U14 (EHRPWM1A_U14); also elsewhere on the board
PWM_1B: SIP.T14 (EHRPWM1B_T14); also elsewhere on the board
PWM_2A: SIP.U10 (EHRPWM2A_U10); also elsewhere on the board
PWM_2B: SIP.T10 (EHRPWM2B_T10); also elsewhere on the board
PWR_LED: ON.C, R24.1
RESET: C33.1, R60.1, SIP.A10 (WARMRSTN), U6.4 (Y); also elsewhere on the board
SPI1_MISO: SIP.B13 (SPI1_D0_B13); also elsewhere on the board
SPI1_MOSI: SIP.D12 (SPI1_D1_D12); also elsewhere on the board
SPI1_SCK: SIP.A13 (SPI1_CLK_A13); also elsewhere on the board
SPI1_SS2: SIP.C18 (GPIO0_7_C18); also elsewhere on the board
SYS_5V: SIP.W4 (VOUT_SYS_5V_0), SIP.Y4 (VOUT_SYS_5V_1), TP1.TP, U1.3 (VCC); also elsewhere on the board
UART0_RX: SIP.E15 (UART0_RXD_E15); also elsewhere on the board
UART0_TX: SIP.E16 (UART0_TXD_E16); also elsewhere on the board
UART1_RX: SIP.D16 (UART1_RXD_D16); also elsewhere on the board
UART1_TX: SIP.D15 (UART1_TXD_D15); also elsewhere on the board
UART2_RX: SIP.A17 (UART2_RXD_A17); also elsewhere on the board
UART2_TX: SIP.B17 (UART2_TXD_B17); also elsewhere on the board
UART4_RX: SIP.T17 (UART4_RXD_T17); also elsewhere on the board
USB_DC: SIP.Y8 (VIN_USB_0), SIP.Y9 (VIN_USB_1); also elsewhere on the board
USR_LED0: SIP.V15 (USR0_V15); also elsewhere on the board
USR_LED1: SIP.U15 (USR1_U15); also elsewhere on the board
USR_LED2: SIP.T15 (USR2_T15); also elsewhere on the board
USR_LED3: SIP.V16 (USR3_V16); also elsewhere on the board
VDD_1V8: SIP.N16 (VOUT_LDO3_1P8V_0), SIP.R16 (VOUT_LDO3_1P8V_1); also elsewhere on the board
VDD_3V3AUX: ON.A, SIP.Y11 (VOUT_LDO2_3P3V)
VDD_RTC: U6.5 (VCC); also elsewhere on the board
VIN_BAT_0: SIP.Y2 (VIN_BAT_0)
VIN_BAT_1: SIP.Y3 (VIN_BAT_1)
WIFI_LED: SIP.A15 (GPIO0_19_A15); also elsewhere on the board

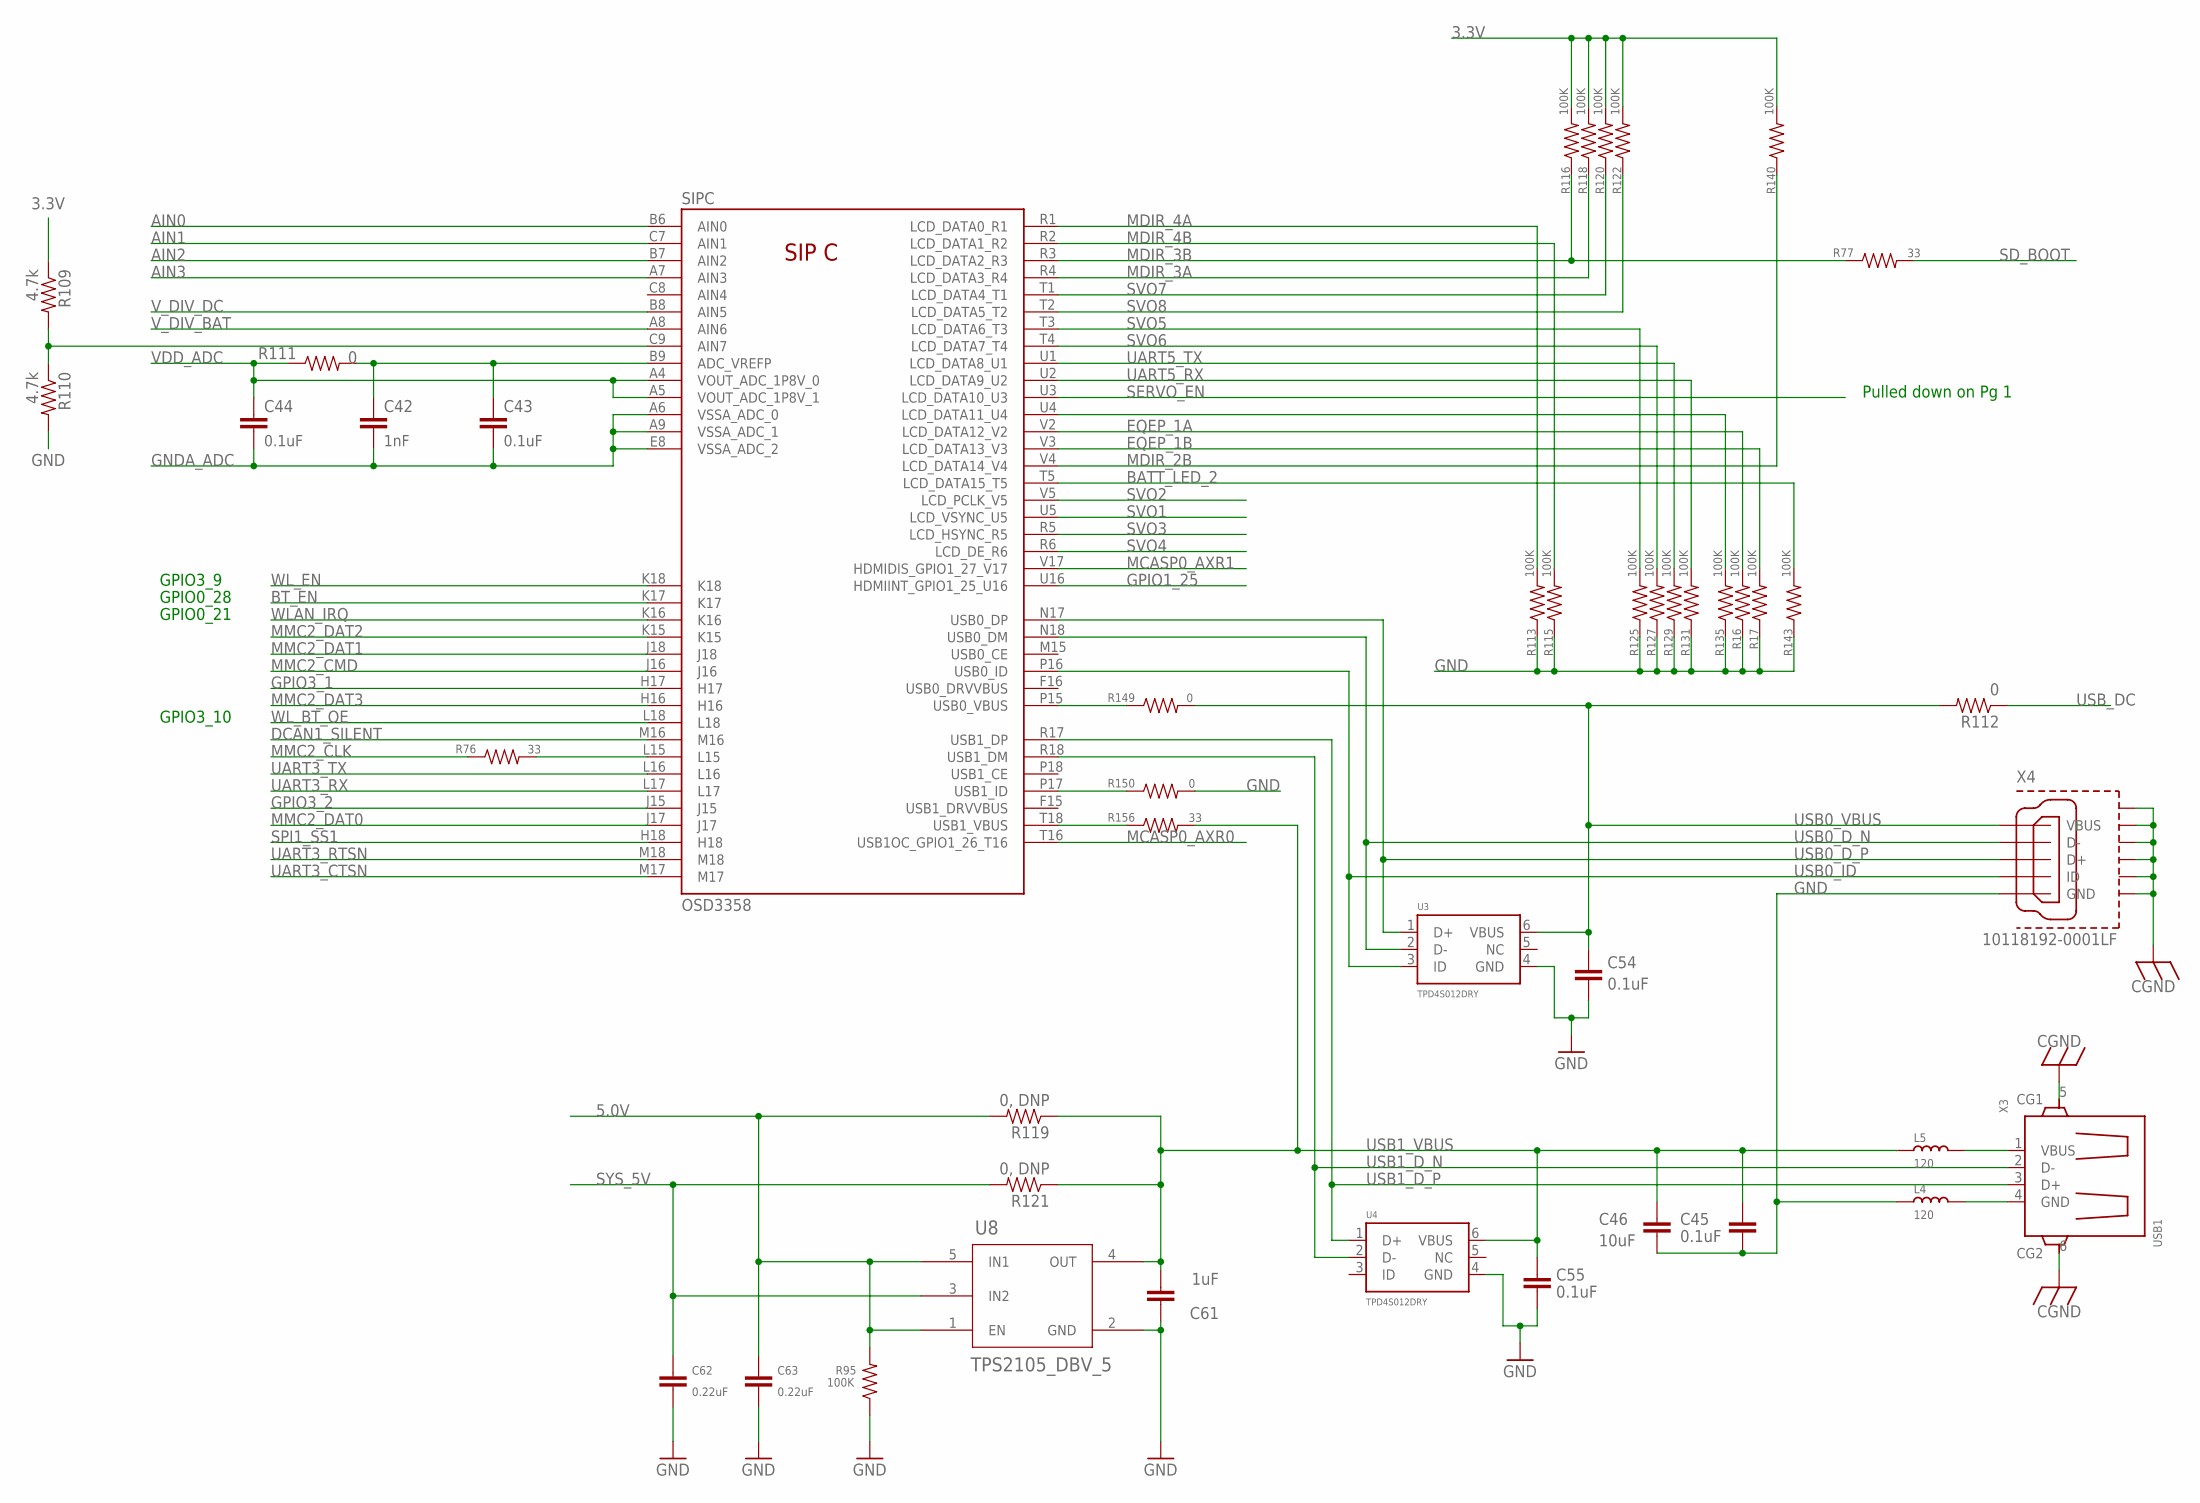
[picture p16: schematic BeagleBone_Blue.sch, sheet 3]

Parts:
C42: 1nF; 0402-CAP
C43, C44, C45, C54, C55: 0.1uF; 0402-CAP
C46: 10uF; 0805
C61: 1uF; 0402-CAP
C62, C63: 0.22uF; 0402-CAP
L4, L5: 120; L0603
R16, R17, R95, R113, R115, R116, R118, R120, R122, R125, R127, R129, R131, R135, R140, R143: 100K; 0402-RES
R76, R77, R156: 33; 0402-RES
R109, R110: 4.7k; 0402-RES
R111, R149, R150: 0; 0402-RES
R112: 0; 0603-RES
R119, R121: 0, DNP; 0603-RES
SIP: OSD3358; BEAGLEBONE_BLUE_OSD3358
U3, U4: TPD4S012DRY; SON-6(TI)-DRY
U8: TPS2105_DBV_5; DBV5
X3: USB1; USB_HOST_HORIZONTAL_W/CHASSIS_GND
X4: 10118192-0001LF; 10118192-0001LF(MICRO-USB-B-AMPHENOL-FCI)

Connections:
3.3V: R109.1, R116.2, R118.2, R120.2, R122.2, R140.2; also elsewhere on the board
5.0V: C63.1, R95.2, R119.2, U8.1 (EN), U8.5 (IN1); also elsewhere on the board
AIN0: SIP.B6 (AIN0); also elsewhere on the board
AIN1: SIP.C7 (AIN1); also elsewhere on the board
AIN2: SIP.B7 (AIN2); also elsewhere on the board
AIN3: SIP.A7 (AIN3); also elsewhere on the board
BATT_LED_2: R143.2, SIP.T5 (LCD_DATA15_T5); also elsewhere on the board
BT_EN: SIP.K17; also elsewhere on the board
CGND: X3.5 (CG1), X3.6 (CG2), X4.CGND1 (SGND1), X4.CGND2 (SGND2), X4.CGND3 (SGND3), X4.CGND4 (SGND4), X4.CGND5 (SGND5), X4.CGND6 (SGND6); also elsewhere on the board
DCAN1_SILENT: SIP.M16; also elsewhere on the board
EQEP_1A: R16.2, SIP.V2 (LCD_DATA12_V2); also elsewhere on the board
EQEP_1B: R17.2, SIP.V3 (LCD_DATA13_V3); also elsewhere on the board
GND: C45.2, C46.2, C54.2, C55.2, C61.1, C62.2, C63.2, L4.1, R16.1, R17.1, R95.1, R110.2, R113.1, R115.1, R125.1, R127.1, R129.1, R131.1, R135.1, R143.1, R150.2, U3.4 (GND), U4.4 (GND), U8.2 (GND), X4.GND; also elsewhere on the board
GNDA_ADC: C42.2, C43.2, C44.2, SIP.A6 (VSSA_ADC_0), SIP.A9 (VSSA_ADC_1), SIP.E8 (VSSA_ADC_2)
GPIO1_25: SIP.U16 (HDMIINT_GPIO1_25_U16); also elsewhere on the board
GPIO3_1: SIP.H17; also elsewhere on the board
GPIO3_2: SIP.J15; also elsewhere on the board
MCASP0_AXR0: SIP.T16 (USB1OC_GPIO1_26_T16); also elsewhere on the board
MCASP0_AXR1: SIP.V17 (HDMIDIS_GPIO1_27_V17); also elsewhere on the board
MDIR_2B: R140.1, SIP.V4 (LCD_DATA14_V4); also elsewhere on the board
MDIR_3A: R118.1, SIP.R4 (LCD_DATA3_R4); also elsewhere on the board
MDIR_3B: R77.1, R116.1, SIP.R3 (LCD_DATA2_R3); also elsewhere on the board
MDIR_4A: R113.2, SIP.R1 (LCD_DATA0_R1); also elsewhere on the board
MDIR_4B: R115.2, SIP.R2 (LCD_DATA1_R2); also elsewhere on the board
MMC2_CLK: R76.1; also elsewhere on the board
MMC2_CMD: SIP.J16; also elsewhere on the board
MMC2_DAT0: SIP.J17; also elsewhere on the board
MMC2_DAT1: SIP.J18; also elsewhere on the board
MMC2_DAT2: SIP.K15; also elsewhere on the board
MMC2_DAT3: SIP.H16; also elsewhere on the board
unnamed: R76.2, SIP.L15
unnamed: R135.2, SIP.U4 (LCD_DATA11_U4)
unnamed: C42.1, C43.1, R111.2, SIP.B9 (ADC_VREFP)
unnamed: R109.2, R110.1, SIP.C9 (AIN7)
unnamed: R149.1, SIP.P15 (USB0_VBUS)
unnamed: R150.1, SIP.P17 (USB1_ID)
unnamed: L4.2, X3.4 (GND)
unnamed: R156.1, SIP.T18 (USB1_VBUS)
unnamed: L5.2, X3.1 (VBUS)
SD_BOOT: R77.2; also elsewhere on the board
SERVO_EN: SIP.U3 (LCD_DATA10_U3); also elsewhere on the board
SPI1_SS1: SIP.H18; also elsewhere on the board
SVO1: SIP.U5 (LCD_VSYNC_U5); also elsewhere on the board
SVO2: SIP.V5 (LCD_PCLK_V5); also elsewhere on the board
SVO3: SIP.R5 (LCD_HSYNC_R5); also elsewhere on the board
SVO4: SIP.R6 (LCD_DE_R6); also elsewhere on the board
SVO5: R125.2, SIP.T3 (LCD_DATA6_T3); also elsewhere on the board
SVO6: R127.2, SIP.T4 (LCD_DATA7_T4); also elsewhere on the board
SVO7: R120.1, SIP.T1 (LCD_DATA4_T1); also elsewhere on the board
SVO8: R122.1, SIP.T2 (LCD_DATA5_T2); also elsewhere on the board
SYS_5V: C62.1, R121.2, U8.3 (IN2); also elsewhere on the board
UART3_CTSN: SIP.M17; also elsewhere on the board
UART3_RTSN: SIP.M18; also elsewhere on the board
UART3_RX: SIP.L17; also elsewhere on the board
UART3_TX: SIP.L16; also elsewhere on the board
UART5_RX: R131.2, SIP.U2 (LCD_DATA9_U2); also elsewhere on the board
UART5_TX: R129.2, SIP.U1 (LCD_DATA8_U1); also elsewhere on the board
USB0_D_N: SIP.N18 (USB0_DM), U3.2 (D-), X4.D-
USB0_D_P: SIP.N17 (USB0_DP), U3.1 (D+), X4.D+
USB0_ID: SIP.P16 (USB0_ID), U3.3 (ID), X4.ID
USB0_VBUS: C54.1, R112.2, R149.2, U3.6 (VBUS), X4.VBUS
USB1_D_N: SIP.R18 (USB1_DM), U4.2 (D-), X3.2 (D-)
USB1_D_P: SIP.R17 (USB1_DP), U4.1 (D+), X3.3 (D+)
USB1_VBUS: C45.1, C46.1, C55.1, C61.2, L5.1, R119.1, R121.1, R156.2, U4.6 (VBUS), U8.4 (OUT)
USB_DC: R112.1; also elsewhere on the board
VDD_ADC: C44.1, R111.1, SIP.A4 (VOUT_ADC_1P8V_0), SIP.A5 (VOUT_ADC_1P8V_1); also elsewhere on the board
VIN_BAT_0: SIP.Y2 (VIN_BAT_0)
VIN_BAT_1: SIP.Y3 (VIN_BAT_1)
V_DIV_BAT: SIP.A8 (AIN6); also elsewhere on the board
V_DIV_DC: SIP.B8 (AIN5); also elsewhere on the board
WLAN_IRQ: SIP.K16; also elsewhere on the board
WL_BT_OE: SIP.L18; also elsewhere on the board
WL_EN: SIP.K18; also elsewhere on the board

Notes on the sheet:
Pulled down on Pg 1
GPIO3_9
GPIO0_28
GPIO0_21
GPIO3_10

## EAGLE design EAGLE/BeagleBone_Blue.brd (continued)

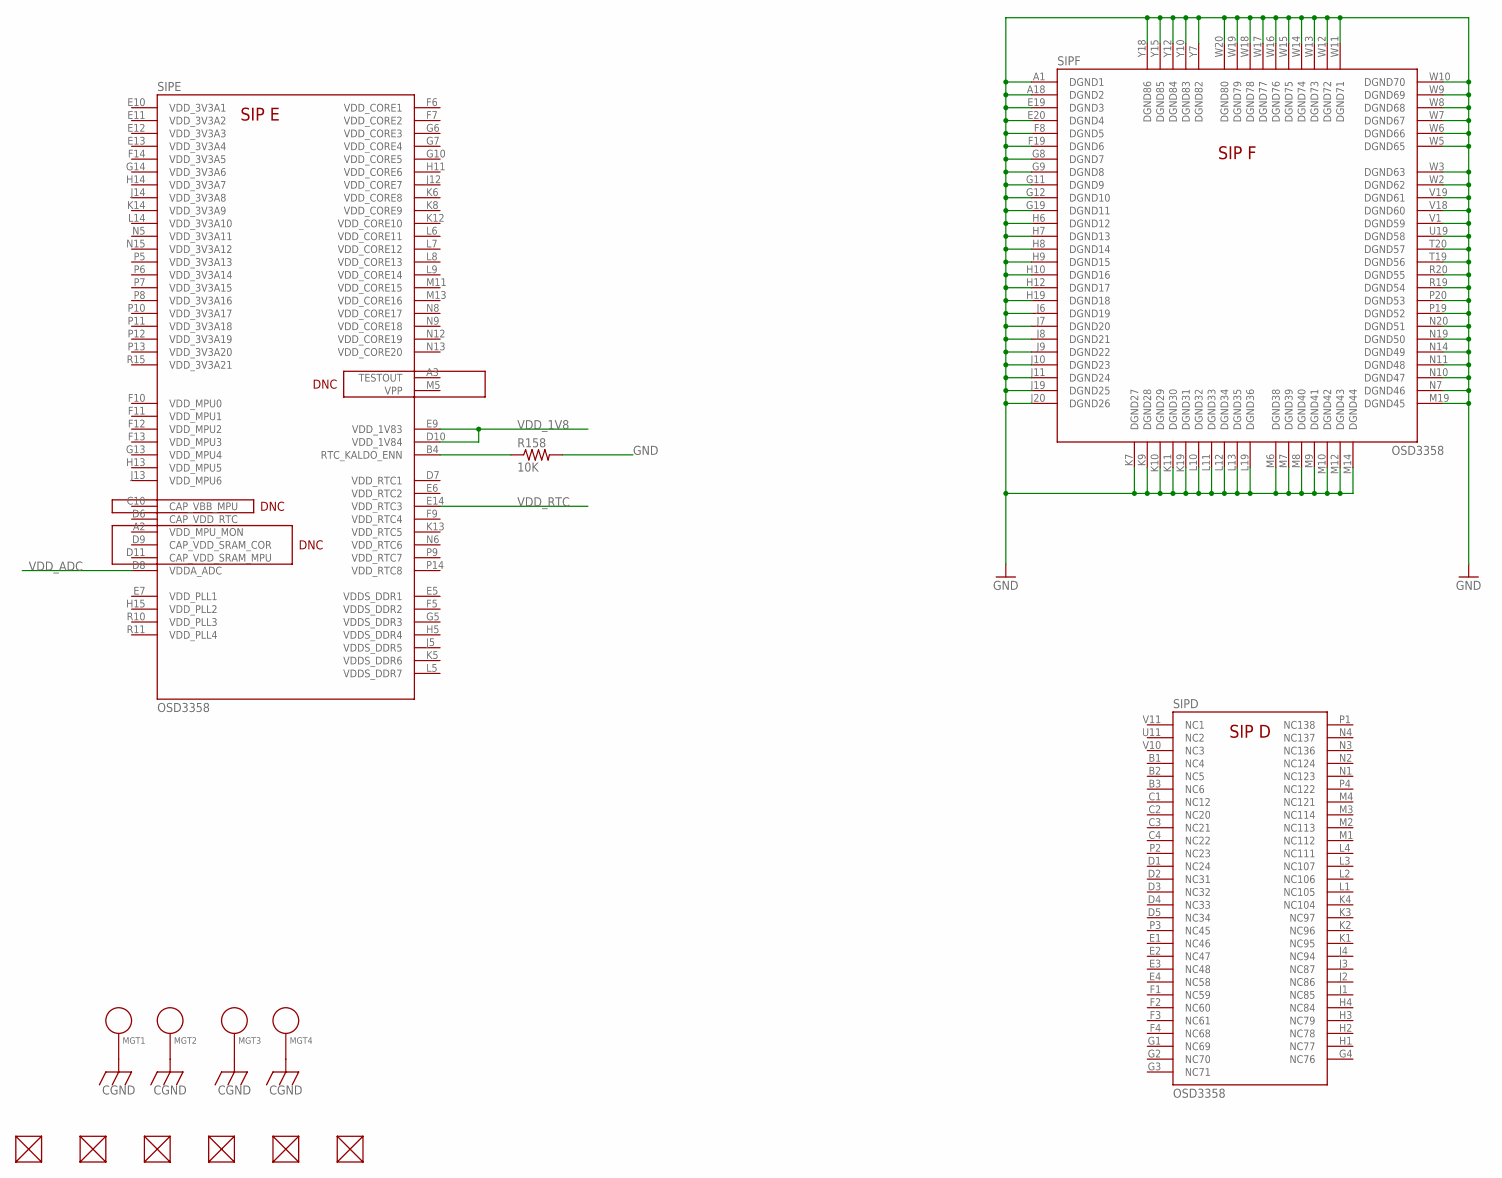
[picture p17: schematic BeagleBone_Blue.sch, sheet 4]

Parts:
FUD1, FUD2, FUD3, FUD4, FUD5, FUD6: FIDUCIAL; FIDUCIAL_40MIL
MGT1, MGT2, MGT3, MGT4: MOUNTING_HOLE
R158: 10K; 0402-RES
SIP: OSD3358; BEAGLEBONE_BLUE_OSD3358

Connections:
CGND: MGT1.P$1, MGT2.P$1, MGT3.P$1, MGT4.P$1; also elsewhere on the board
GND: R158.2, SIP.A1 (DGND1), SIP.A18 (DGND2), SIP.E19 (DGND3), SIP.E20 (DGND4), SIP.F8 (DGND5), SIP.F19 (DGND6), SIP.G8 (DGND7), SIP.G9 (DGND8), SIP.G11 (DGND9), SIP.G12 (DGND10), SIP.G19 (DGND11), SIP.H6 (DGND12), SIP.H7 (DGND13), SIP.H8 (DGND14), SIP.H9 (DGND15), SIP.H10 (DGND16), SIP.H12 (DGND17), SIP.H19 (DGND18), SIP.J6 (DGND19), SIP.J7 (DGND20), SIP.J8 (DGND21), SIP.J9 (DGND22), SIP.J10 (DGND23), SIP.J11 (DGND24), SIP.J19 (DGND25), SIP.J20 (DGND26), SIP.K7 (DGND27), SIP.K9 (DGND28), SIP.K10 (DGND29), SIP.K11 (DGND30), SIP.K19 (DGND31), SIP.L10 (DGND32), SIP.L11 (DGND33), SIP.L12 (DGND34), SIP.L13 (DGND35), SIP.L19 (DGND36), SIP.M6 (DGND38), SIP.M7 (DGND39), SIP.M8 (DGND40), SIP.M9 (DGND41), SIP.M10 (DGND42), SIP.M12 (DGND43), SIP.M14 (DGND44), SIP.M19 (DGND45), SIP.N7 (DGND46), SIP.N10 (DGND47), SIP.N11 (DGND48), SIP.N14 (DGND49), SIP.N19 (DGND50), SIP.N20 (DGND51), SIP.P19 (DGND52), SIP.P20 (DGND53), SIP.R19 (DGND54), SIP.R20 (DGND55), SIP.T19 (DGND56), SIP.T20 (DGND57), SIP.U19 (DGND58), SIP.V1 (DGND59), SIP.V18 (DGND60), SIP.V19 (DGND61), SIP.W2 (DGND62), SIP.W3 (DGND63), SIP.W5 (DGND65), SIP.W6 (DGND66), SIP.W7 (DGND67), SIP.W8 (DGND68), SIP.W9 (DGND69), SIP.W10 (DGND70), SIP.W11 (DGND71), SIP.W12 (DGND72), SIP.W13 (DGND73), SIP.W14 (DGND74), SIP.W15 (DGND75), SIP.W16 (DGND76), SIP.W17 (DGND77), SIP.W18 (DGND78), SIP.W19 (DGND79), SIP.W20 (DGND80), SIP.Y7 (DGND82), SIP.Y10 (DGND83), SIP.Y12 (DGND84), SIP.Y15 (DGND85), SIP.Y18 (DGND86); also elsewhere on the board
unnamed: R158.1, SIP.B4 (RTC_KALDO_ENN)
VDD_1V8: SIP.D10 (VDD_1V84), SIP.E9 (VDD_1V83); also elsewhere on the board
VDD_ADC: SIP.D8 (VDDA_ADC); also elsewhere on the board
VDD_RTC: SIP.E14 (VDD_RTC3); also elsewhere on the board
VIN_BAT_0: SIP.Y2 (VIN_BAT_0)
VIN_BAT_1: SIP.Y3 (VIN_BAT_1)

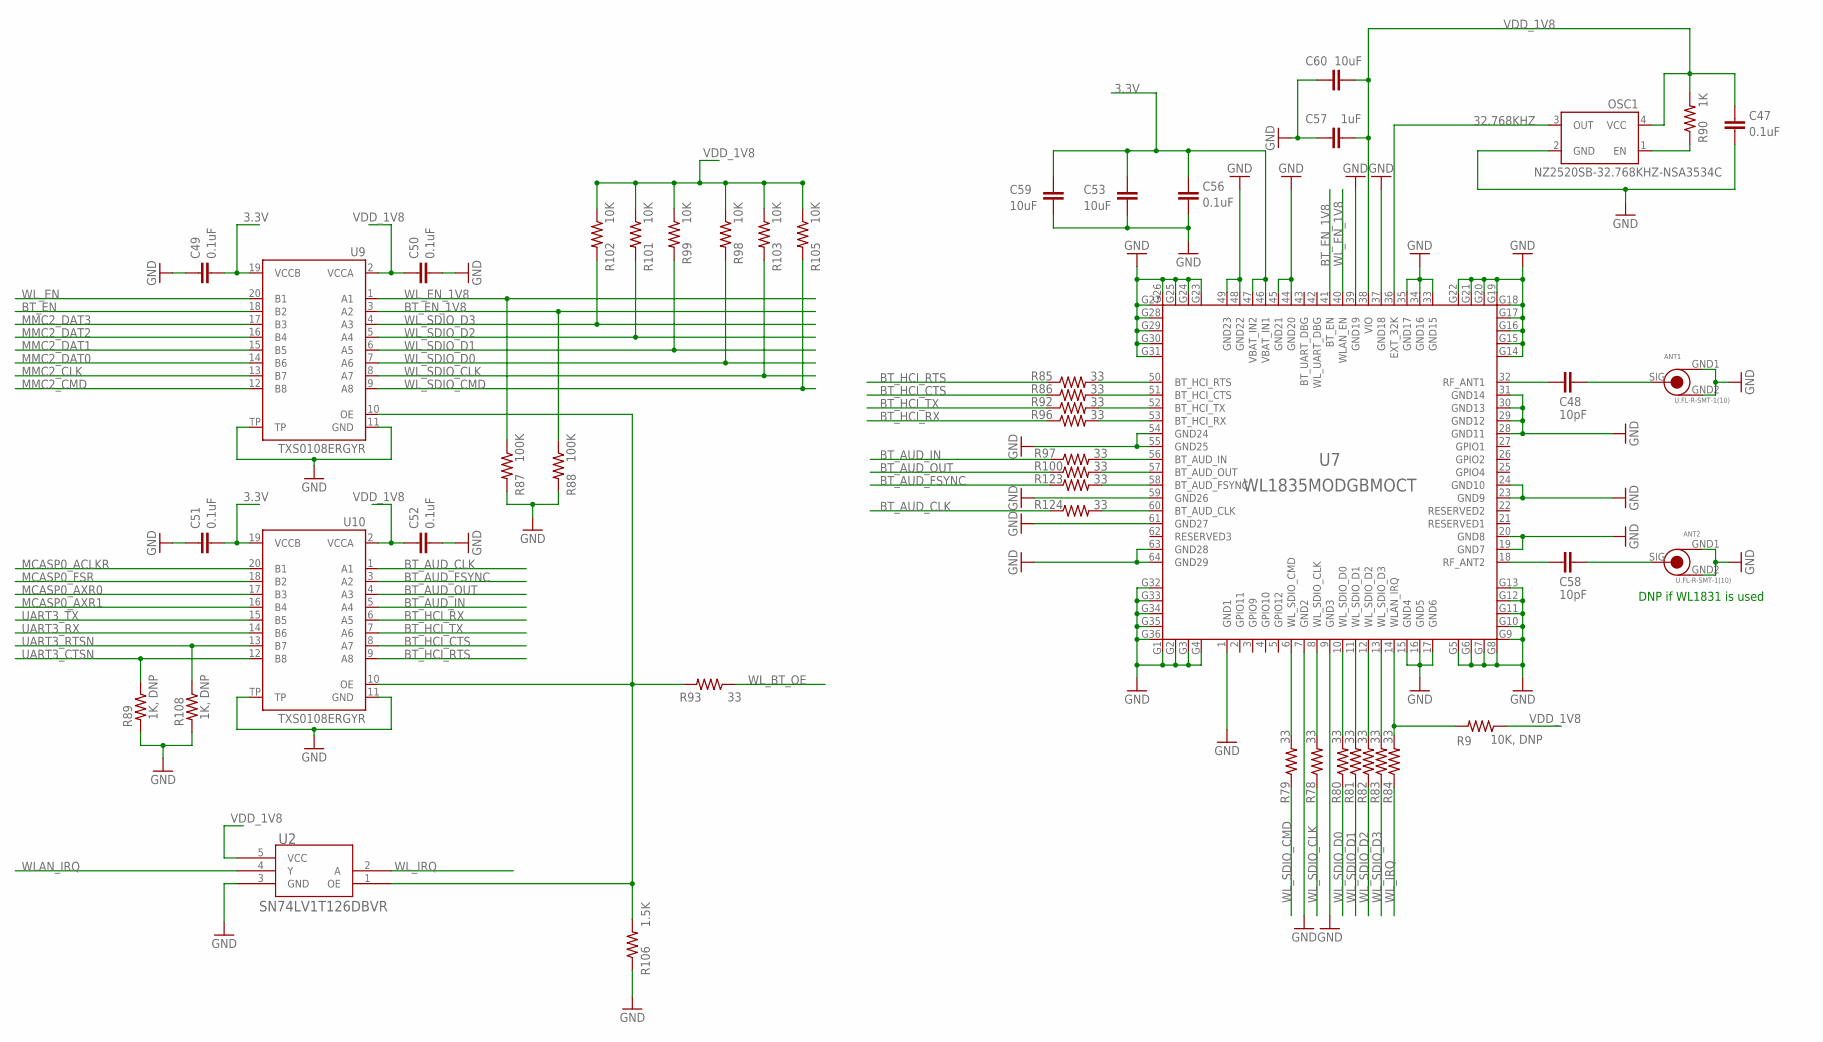
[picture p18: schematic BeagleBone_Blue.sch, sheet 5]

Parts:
ANT1, ANT2: U.FL-R-SMT-1(10); U.FL-R-SMT-1
C47, C49, C50, C51, C52, C56: 0.1uF; 0402-CAP
C48, C58: 10pF; 0402-CAP
C53, C59, C60: 10uF; 0805
C57: 1uF; 0402-CAP
OSC1: NZ2520SB-32.768KHZ-NSA3534C; NZ2520S
R9: 10K, DNP; 0402-RES
R78, R79, R80, R81, R82, R83, R84, R85, R86, R92, R93, R96, R97, R100, R123, R124: 33; 0402-RES
R87, R88: 100K; 0402-RES
R89, R108: 1K, DNP; 0402-RES
R90: 1K; 0402-RES
R98, R99, R101, R102, R103, R105: 10K; 0402-RES
R106: 1.5K; 0402-RES
U2: SN74LV1T126DBVR; BEAGLEBONE_BLUE_SOT23-5
U7: WL1835MODGBMOCT; MOC-100(TI)
U9, U10: TXS0108ERGYR; R-PVQFN-N20(TI)

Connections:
3.3V: C49.2, C51.2, C53.1, C56.1, C59.1, U7.46 (VBAT_IN1), U7.47 (VBAT_IN2), U9.19 (VCCB), U10.19 (VCCB); also elsewhere on the board
32.768KHZ: OSC1.3 (OUT), U7.36 (EXT_32K)
ALT.BUFF.OE: R93.2, R106.2, U2.1 (OE), U9.10 (OE), U10.10 (OE)
ANT1_A: C48.2, U7.32 (RF_ANT1)
ANT1_B: ANT1.SIG, C48.1
ANT2_A: C58.2, U7.18 (RF_ANT2)
ANT2_B: ANT2.SIG, C58.1
BT_AUD_CLK: R124.1, U10.1 (A1)
BT_AUD_FSYNC: R123.1, U10.3 (A2)
BT_AUD_IN: R97.1, U10.5 (A4)
BT_AUD_OUT: R100.1, U10.4 (A3)
BT_EN: U9.18 (B2); also elsewhere on the board
BT_EN_1V8: R88.1, U7.41 (BT_EN), U9.3 (A2)
BT_HCI_CTS: R86.1, U10.8 (A7)
BT_HCI_RTS: R85.1, U10.9 (A8)
BT_HCI_RX: R96.1, U10.6 (A5)
BT_HCI_TX: R92.1, U10.7 (A6)
GND: ANT1.GND1, ANT1.GND2, ANT2.GND1, ANT2.GND2, C47.2, C49.1, C50.2, C51.1, C52.2, C53.2, C56.2, C57.1, C59.2, C60.1, OSC1.2 (GND), R87.2, R88.2, R89.2, R106.1, R108.2, U2.3 (GND), U7.1 (GND1), U7.7 (GND2), U7.9 (GND3), U7.15 (GND4), U7.16 (GND5), U7.17 (GND6), U7.19 (GND7), U7.20 (GND8), U7.23 (GND9), U7.24 (GND10), U7.28 (GND11), U7.29 (GND12), U7.30 (GND13), U7.31 (GND14), U7.33 (GND15), U7.34 (GND16), U7.35 (GND17), U7.37 (GND18), U7.39 (GND19), U7.44 (GND20), U7.45 (GND21), U7.48 (GND22), U7.49 (GND23), U7.54 (GND24), U7.55 (GND25), U7.59 (GND26), U7.61 (GND27), U7.63 (GND28), U7.64 (GND29), U7.G1, U7.G2, U7.G3, U7.G4, U7.G5, U7.G6, U7.G7, U7.G8, U7.G9, U7.G10, U7.G11, U7.G12, U7.G13, U7.G14, U7.G15, U7.G16, U7.G17, U7.G18, U7.G19, U7.G20, U7.G21, U7.G22, U7.G23, U7.G24, U7.G25, U7.G26, U7.G27, U7.G28, U7.G29, U7.G30, U7.G31, U7.G32, U7.G33, U7.G34, U7.G35, U7.G36, U9.11 (GND), U9.TP, U10.11 (GND), U10.TP; also elsewhere on the board
MCASP0_ACLKR: U10.20 (B1); also elsewhere on the board
MCASP0_AXR0: U10.17 (B3); also elsewhere on the board
MCASP0_AXR1: U10.16 (B4); also elsewhere on the board
MCASP0_FSR: U10.18 (B2); also elsewhere on the board
MMC2_CLK: U9.13 (B7); also elsewhere on the board
MMC2_CMD: U9.12 (B8); also elsewhere on the board
MMC2_DAT0: U9.14 (B6); also elsewhere on the board
MMC2_DAT1: U9.15 (B5); also elsewhere on the board
MMC2_DAT2: U9.16 (B4); also elsewhere on the board
MMC2_DAT3: U9.17 (B3); also elsewhere on the board
unnamed: OSC1.1 (EN), R90.1
unnamed: R100.2, U7.57 (BT_AUD_OUT)
unnamed: R9.2, R84.2, U7.14 (WLAN_IRQ)
unnamed: R83.2, U7.13 (WL_SDIO_D3)
unnamed: R82.2, U7.12 (WL_SDIO_D2)
unnamed: R81.2, U7.11 (WL_SDIO_D1)
unnamed: R80.2, U7.10 (WL_SDIO_D0)
unnamed: R78.2, U7.8 (WL_SDIO_CLK)
unnamed: R79.2, U7.6 (WL_SDIO_CMD)
unnamed: R85.2, U7.50 (BT_HCI_RTS)
unnamed: R86.2, U7.51 (BT_HCI_CTS)
unnamed: R92.2, U7.52 (BT_HCI_TX)
unnamed: R96.2, U7.53 (BT_HCI_RX)
unnamed: R97.2, U7.56 (BT_AUD_IN)
unnamed: R123.2, U7.58 (BT_AUD_FSYNC)
unnamed: R124.2, U7.60 (BT_AUD_CLK)
UART3_CTSN: R89.1, U10.12 (B8); also elsewhere on the board
UART3_RTSN: R108.1, U10.13 (B7); also elsewhere on the board
UART3_RX: U10.14 (B6); also elsewhere on the board
UART3_TX: U10.15 (B5); also elsewhere on the board
VDD_1V8: C47.1, C50.1, C52.1, C57.2, C60.2, OSC1.4 (VCC), R9.1, R90.2, R98.1, R99.1, R101.1, R102.1, R103.1, R105.1, U2.5 (VCC), U7.38 (VIO), U9.2 (VCCA), U10.2 (VCCA); also elsewhere on the board
WLAN_IRQ: U2.4 (Y); also elsewhere on the board
WL_BT_OE: R93.1; also elsewhere on the board
WL_EN: U9.20 (B1); also elsewhere on the board
WL_EN_1V8: R87.1, U7.40 (WLAN_EN), U9.1 (A1)
WL_IRQ: R84.1, U2.2 (A)
WL_SDIO_CLK: R78.1, R103.2, U9.8 (A7)
WL_SDIO_CMD: R79.1, R105.2, U9.9 (A8)
WL_SDIO_D0: R80.1, R98.2, U9.7 (A6)
WL_SDIO_D1: R81.1, R99.2, U9.6 (A5)
WL_SDIO_D2: R82.1, R101.2, U9.5 (A4)
WL_SDIO_D3: R83.1, R102.2, U9.4 (A3)

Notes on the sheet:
DNP if WL1831 is used

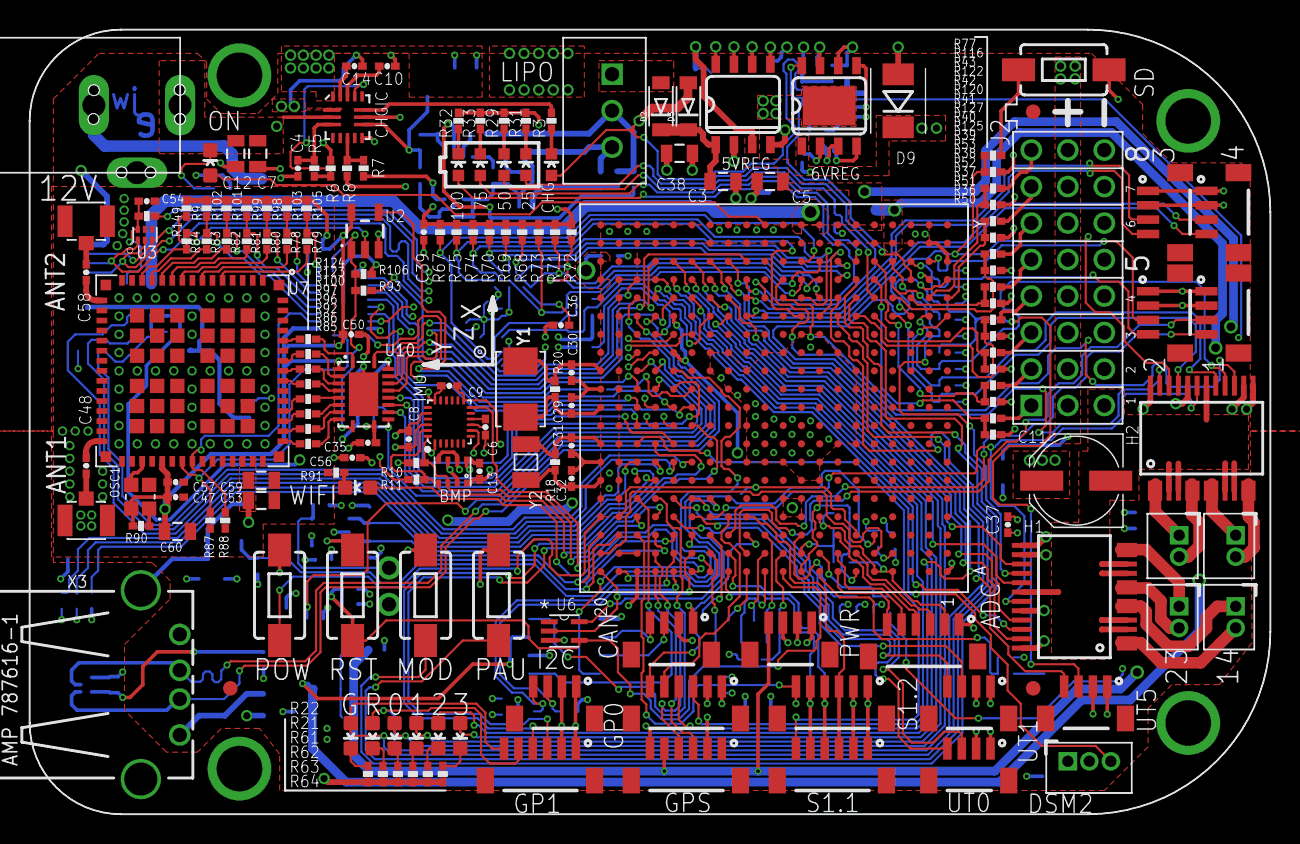
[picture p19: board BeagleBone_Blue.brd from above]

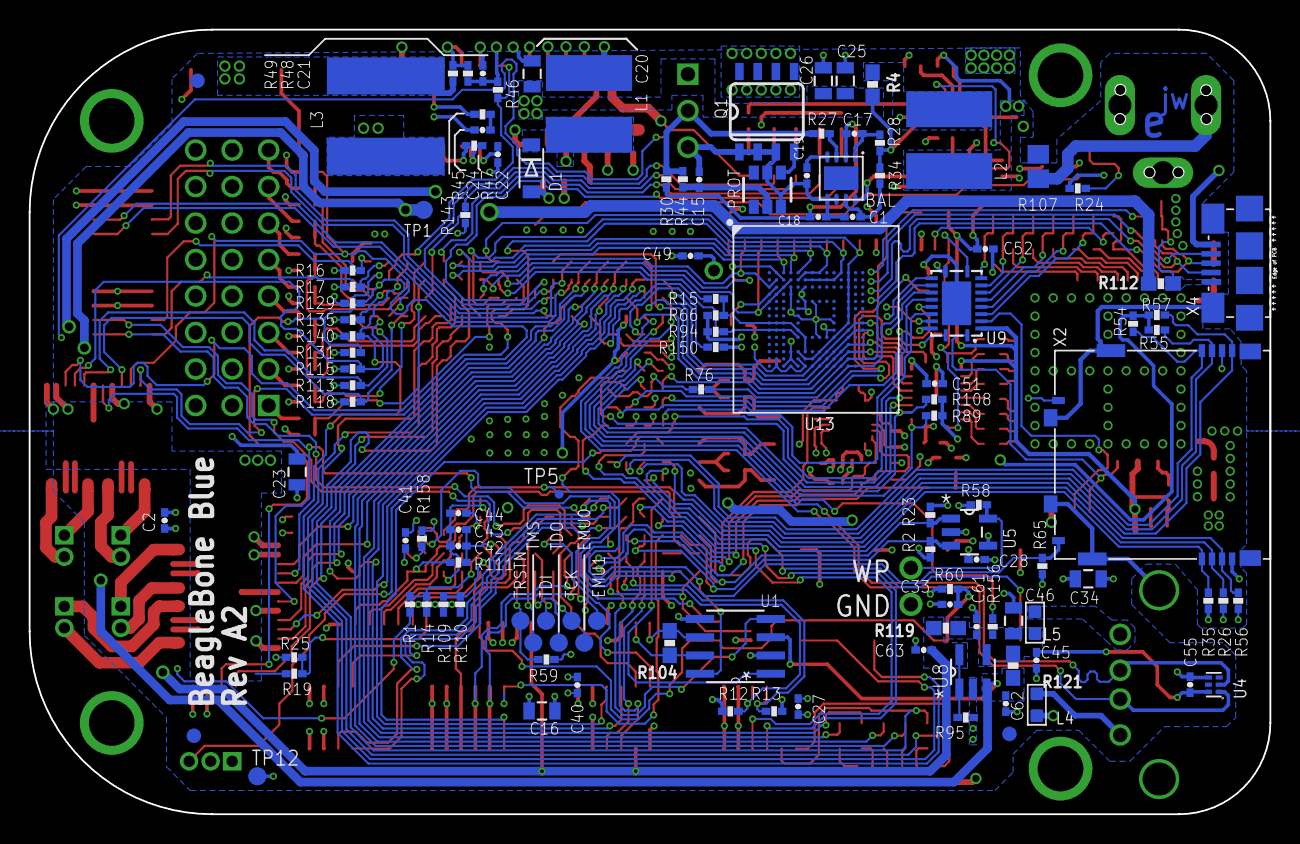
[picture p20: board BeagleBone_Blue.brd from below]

Board: 4 copper layers, 86.4 x 54.6 mm, 302 parts (122 on the bottom side), 268 nets.

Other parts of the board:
BOARD: BEAGLEBONE_BLUE_NO_HOLES
U$2: BATTERY_INDICATOR_LEFT
U$5: XYZ_BIG

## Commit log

2015-08-23 added Cape BOM & Header Pin Table
    [SD-101D Robotics Cape BOM.xlsx, SD-101D Robotics Cape Header Pin Table .xlsx]
2015-08-30 initial shuffling of Robotics Cape components.
    [BeagleBone Blue.brd, BeagleBone Blue.sch]
2015-09-02 BeagleBone Black in EAGLE from Element14
    [BeagleBone_Black_Rev C EAGLE PCB.brd, BeagleBone_Black_Rev C EAGLE PCB.sch]
2015-09-14 move Hbridges to back
    [BeagleBone Blue.brd]
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2015-10-21 Add initial board from BeagleBone Black
    [BeagleBone_Blue.brd]
2015-10-21 Removed some unused components
    [BeagleBone_Blue.brd]
2015-10-22 Updates based on review
    [BeagleBone_Blue.brd, BeagleBone_Blue.sch]
2015-10-28 add pulldowns on servo channels
    [BeagleBone_Blue.sch]
2015-10-28 added new pin table, xlsx move SPI1_SS2
    [BeagleBone Blue Pin Table.xlsx]
2015-10-28 split C18 & B12 which were connected on the cape
    [BeagleBone_Blue.sch]
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2015-11-02 move new SD-101D files to the reference documents folder
    [SD-101D Robotics Cape BOM.xlsx, SD-101D Robotics Cape.brd, SD-101D Robotics Cape.sch]
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2015-11-09 Remove SD card slot and Label SDIO&UART5 for WIFi use on page 9
    [BeagleBone Blue Pin Table.xlsx, BeagleBone_Blue.sch]
2015-11-09 reserve last gpio pins for WIFI_EN and BT_EN
    [BeagleBone_Blue.sch]
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2015-11-11 cleanup all the nonsense import errors from the EAGLE board conversion
    [BeagleBone_Blue.brd]
2015-11-11 swap mini usb for micro usb
    [BeagleBone_Blue.sch]
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2015-11-11 remove and put robotics cape components back to try to fix ERC errors. failed. :(
    [BeagleBone_Blue.sch]
2015-11-11 Make new BOM sorted by parts, incomplete due to ERC errors
    [BeagleBone_Blue BOM by Parts.xlsx, BeagleBone_Blue.sch]
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2015-11-18 Replace title block
    [BeagleBone_Blue.DSN]
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2015-12-03 Pin usage updates * UART3, MMC2 and MCASP0 for WiFi/Bluetooth * Enumerate additional pins not listed on the expansion header
    [BeagleBone Blue Pin Table.xlsx]
2015-12-03 Partial label fixes
    [BeagleBone_Blue.DSN]
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2015-12-04 Use Cape reference as new EAGLE Blue starting point
    [BeagleBone_Blue.brd, BeagleBone_Blue.sch]
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2015-12-06 Fix some ERCs
    [BeagleBone_Blue.brd]
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2015-12-11 Fixing some ERCs
    [BeagleBone_Blue.brd, BeagleBone_Blue.sch]
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2015-12-14 Cleared all errors
    [BeagleBone_Blue.brd, BeagleBone_Blue.sch]
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2015-12-15 Rough placed a few parts and print schematic
    [BeagleBone_Blue.brd]
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2015-12-16 change DSM2 connector to surface mount & move buttons
    [BeagleBone_Blue.brd, BeagleBone_Blue.sch]
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2015-12-16 swap to MicroUSB connector
    [BeagleBone_Blue.brd, BeagleBone_Blue.sch]
2015-12-16 shuffle left side of board and tweak silkscreen for EEPROM
    [BeagleBone_Blue.brd, BeagleBone_Blue.sch]
2015-12-16 fix incorrect name and origin for usb host port and capacitor in library
    [BeagleBone_Blue.brd, BeagleBone_Blue.sch]
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2015-12-16 Rename directories to remove spaces and make shorter
    [BeagleBone_Black_Rev C EAGLE PCB.brd, BeagleBone_Black_Rev C EAGLE PCB.sch, BeagleBone_Blue.DSN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]
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2015-12-16 Battery LEDs
    Move resistors to backside
    Rotate LEDs to simplify routing
    [BeagleBone_Blue.brd]
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2015-12-20 Rough place UART0 resistors to avoid uSD cage
    [BeagleBone_Blue.brd]
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2015-12-20 ERC: fix USB ground junction
    [BeagleBone_Blue.sch]
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2015-12-20 DRC fixes
    [BeagleBone_Blue.brd]
2015-12-21 Shuffle some parts to make more room for traces
    [BeagleBone_Blue.brd]
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2015-12-22 Fix VCC
    CHGIC VIN was connected to "5.0V", not VCC.
    [BeagleBone_Blue.sch]
2015-12-22 Remove unpredictable ports
    Used labels and net names rather than power ports
    [BeagleBone_Blue.sch]
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2015-12-23 eMMC pull-ups
    CMD/CLK are pulled up internally by AM335x on reset.
    DATx are pulled down internally by AM335x on reset and are push-pull in
    operation.
    [BeagleBone_Blue.sch]
2015-12-23 In the middle of rearranging the connectors to simplify layout
    [BeagleBone_Blue.brd]
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2015-12-23 Correctly connect VDD_3V3B to 3.3V
    [BeagleBone_Blue.brd, BeagleBone_Blue.sch]
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2015-12-24 Use internal pull-ups for QEP to be applied after boot
    [BeagleBone_Blue.brd, BeagleBone_Blue.sch]
2015-12-24 Fix some DRCs
    [BeagleBone_Blue.brd]
2015-12-24 Crazy position moves trying anything to make it more routable
    [BeagleBone_Blue.brd]
2015-12-24 Try moving LEDs due to the long traces
    [BeagleBone_Blue.brd]
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2015-12-28 Remove eMMC for now since will not route at 5 mil
    [BeagleBone_Blue.brd, BeagleBone_Blue.sch]
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2015-12-29 Swap out uSD connector to one at Sparkfun
    [BeagleBone_Blue.brd, BeagleBone_Blue.sch]
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2015-12-29 Hack 100% autorouted with side connectors on one side
    [BeagleBone_Blue.brd, BeagleBone_Blue.sch]
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2015-12-29 DRC fix
    [BeagleBone_Blue.brd]
2015-12-30 Move uSD to top to try to improve routing
    [BeagleBone_Blue.brd]
2015-12-30 Move uSD back and fix DRCs
    [BeagleBone_Blue.brd]
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2016-01-13 Had added wrong file
    [BeagleBone_Blue.csv]
2016-01-13 Move to an XML format for the BOM
    [BeagleBone_Blue.xlsx]
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2016-01-24 Threw in resistor and capacitor values GHI had handy
    [BeagleBone_Blue.brd, BeagleBone_Blue.sch]
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2016-01-26 swap BMP180 for BMP280 in schematic
    [BeagleBone_Blue.brd, BeagleBone_Blue.sch]
2016-01-26 Open SEL pin on charger to change voltage to 4.2V
    [BeagleBone_Blue.brd, BeagleBone_Blue.sch]
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2016-03-06 Move to an XML pin table to track changes
    [BeagleBone Blue Pin Table.xlsx]
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2016-06-29 Revert "Remove eMMC for now since will not route at 5 mil"
    This reverts commit 75f1e67d3ee9893e94103e41b84841ae77a6b699.
    Conflicts:
    EAGLE_SIP/BeagleBone_Blue.brd
    EAGLE_SIP/BeagleBone_Blue.sch
    [BeagleBone_Blue.brd, BeagleBone_Blue.sch]
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2016-07-19 Fixed I2C EEPROM wiring.
    [BeagleBone_Blue.sch]
2016-07-19 Wired MMC0 pull ups. Moved components on page 1.
    [BeagleBone_Blue.sch]
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2016-07-25 Removed SVO5 - SVO8 pulldown resistors. Conflict w/ bootmode PU/PDs.
    [BeagleBone_Blue.brd, BeagleBone_Blue.sch]
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2016-07-26 Updated clock footprints. Fixed error w/ AM335x clocks.
    [BeagleBone_Blue.brd, BeagleBone_Blue.sch]
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2016-07-27 Fixed V_BATT for 6V reg.
    [BeagleBone_Blue.brd, BeagleBone_Blue.sch]
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2016-07-29 Updated parts: micro SD, micro USB, USB to match BBBW.
    [BeagleBone_Blue.brd, BeagleBone_Blue.sch]
2016-07-29 Added ESD ring; Fixed mouting holes.
    [BeagleBone_Blue.brd, BeagleBone_Blue.sch]
2016-07-31 Updated EMMC componen to match BBBW. Footprint of other component was not routable in 6 mil traces.
    [BeagleBone_Blue.brd, BeagleBone_Blue.sch]
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2016-08-02 replaced some test points with smaller test points.
    [BeagleBone_Blue.brd, BeagleBone_Blue.sch]
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2016-08-11 Fixed power connector footprint. Changed to Rev A1.
    [BeagleBone_Blue.brd, BeagleBone_Blue.sch]
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2016-08-11 Fix missing junction
    [BeagleBone_Blue.sch]
2016-08-11 Fixing Eagle warnings. Warnings were not an issue but cleaning up anyway.
    [BeagleBone_Blue.brd]
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2016-08-30 BRD: move R107 for selective solder
    R107 connects GND to CGND. To solder the power connector (a through-hole component), we'll need to utilize a selective solder machine. That machine needs more clearance not running over surface mount parts. Not sure if this will do it, but I'll check.
    [BeagleBone_Blue.brd]
2016-08-30 Moving R107 and R24 to be farther away from wave soldering parts.
    [BeagleBone_Blue.brd]
2016-08-30 EAGLE: attempt to consolidate library
    I probably have no idea what I'm doing. I'm also concerned I might have messed up D1.
    [BeagleBone_Blue.brd, BeagleBone_Blue.sch]
2016-08-30 EAGLE: more attempts to consolidate library
    I tried to rename some parts to eliminate the prefixes added by the exp-lbrs.ulp script.
    [BeagleBone_Blue.brd, BeagleBone_Blue.sch]
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2016-08-30 Updated layout around USB connector to allow for more space for wave solder.
    [BeagleBone_Blue.brd]
2016-09-07 Fixing silkscreen issues.
    [BeagleBone_Blue.brd, BeagleBone_Blue.sch]
2016-09-20 Fix WL_IRQ GPIO note
    [BeagleBone_Blue.sch]
2016-10-12 Moved R24 and R107 for manufacturing concerns. Cleaned up some power pours on the top and bottom.
    [BeagleBone_Blue.brd]
2016-10-12 Moved L3 for manufacturing issues.
    [BeagleBone_Blue.brd]
2016-10-13 Schematic updates for Rev A2. See Issues.
    [BeagleBone_Blue.brd, BeagleBone_Blue.sch]
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2016-10-18 Intermediate commit; Updated layout; Fixed TPS2105 footprint.
    [BeagleBone_Blue.brd, BeagleBone_Blue.sch]
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2016-10-18 Updated schematics: removed some test points; changed GPIO 1 connector to 6 pin JST; Updated EQEP layout.
    [BeagleBone_Blue.brd, BeagleBone_Blue.sch]
2016-10-18 Updated L1, Q1 for DFM issues from manufacturer.
    [BeagleBone_Blue.brd]
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2016-10-20 Fixed L4, L5 DFM issues; Updated layout.
    [BeagleBone_Blue.brd, BeagleBone_Blue.sch]
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2016-10-26 Updates for DFM issues.
    [BeagleBone_Blue.brd]
2016-10-27 Updated PDF and BOM based on latest schematics.
    [BeagleBone_Blue_BOM.csv]
2016-10-27 Revert "Updated PDF and BOM based on latest schematics."
    This reverts commit 34783d9e17dd36a21b3d147bf87b06cee4abf9bb.
    Erik's commit inadvertently removed all of the carriage returns at the end of hte .CSV file.
    [BeagleBone_Blue_BOM.csv]
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2016-11-02 Gerber update
    * Rename files to match OSH Park "standard"
    * Fix outline by including layer 20
    * Update README.md to describe files
    * Update cam file to reproduce the output
    * Update drill file format precision (was causing OSH Park issues)
    [BeagleBone_Blue.GKO, BeagleBone_Blue.XLN]
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2016-11-22 Adjusted cam file based on OSH Park feedback
    http://support.oshpark.com/support/tickets/29961#
    [BeagleBone_Blue.drills.xln]
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2017-01-16 BeagleBone_Blue.pinmux: fix some pin directions
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2017-01-30 Revert "pull new DCAN and SPI_SS pins from schematic to table"
    This reverts commit 4e067f5e1d7aef13628bb9526eb36e3b84eef1b9.
2017-01-30 Revert "update pin table with new mdir2b and gpio headers"
    This reverts commit f9327dfb45372d406d32ded716de87cc40be3364.
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2017-01-30 Pin table: swap first 2 columns
    [BeagleBone_Blue_Pin_Table.csv]
2017-01-30 Pin table: replace purple with N/C
    [BeagleBone_Blue_Pin_Table.csv]
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2017-02-08 Update BeagleBone_Blue_BOM.csv
    Fix TB6612FNG name
    [BeagleBone_Blue_BOM.csv]
2017-02-28 Update BeagleBone_Blue_BOM.csv
    Tighten up the tolerance on the voltage reading resistors
    [BeagleBone_Blue_BOM.csv]
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2017-03-04 Update PDF schematic to make it searchable (fix_
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2017-09-20 Add motor driver strength
    https://github.com/beagleboard/beaglebone-blue/issues/9
2017-10-20 Issue #8 Motor driver chip is mislabelled pdf
    Updated the PDF with the typo fixed
2017-10-20 Issue #8 Motor driver chip is mislabelled EAGLE
    A global search and replace s/TB6621FNG/TB6612FNG/g of
    the eagle files.
    [BeagleBone_Blue.brd, BeagleBone_Blue.sch]
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

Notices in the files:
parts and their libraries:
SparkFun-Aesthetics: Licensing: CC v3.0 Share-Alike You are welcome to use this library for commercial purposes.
